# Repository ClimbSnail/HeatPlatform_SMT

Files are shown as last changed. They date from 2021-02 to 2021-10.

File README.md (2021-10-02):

# HeatPlatform_SMT
DIY个人分体式SMT平板加热台。ps:二代已经在开发中了 https://github.com/ClimbSnail/SuperHeat

Github项目最新地址[链接](https://github.com/ClimbSnail/HeatPlatform_SMT) https://github.com/ClimbSnail/HeatPlatform_SMT

Gitee地址（可能不是最新的）[链接](https://gitee.com/ClimbSnailQ/HeatPlatform_SMT) https://gitee.com/ClimbSnailQ/HeatPlatform_SMT

Bilibli视频预览[链接](https://www.bilibili.com/video/BV1ky4y1m7ZF) https://www.bilibili.com/video/BV1ky4y1m7ZF

HeatPlatform_Entity

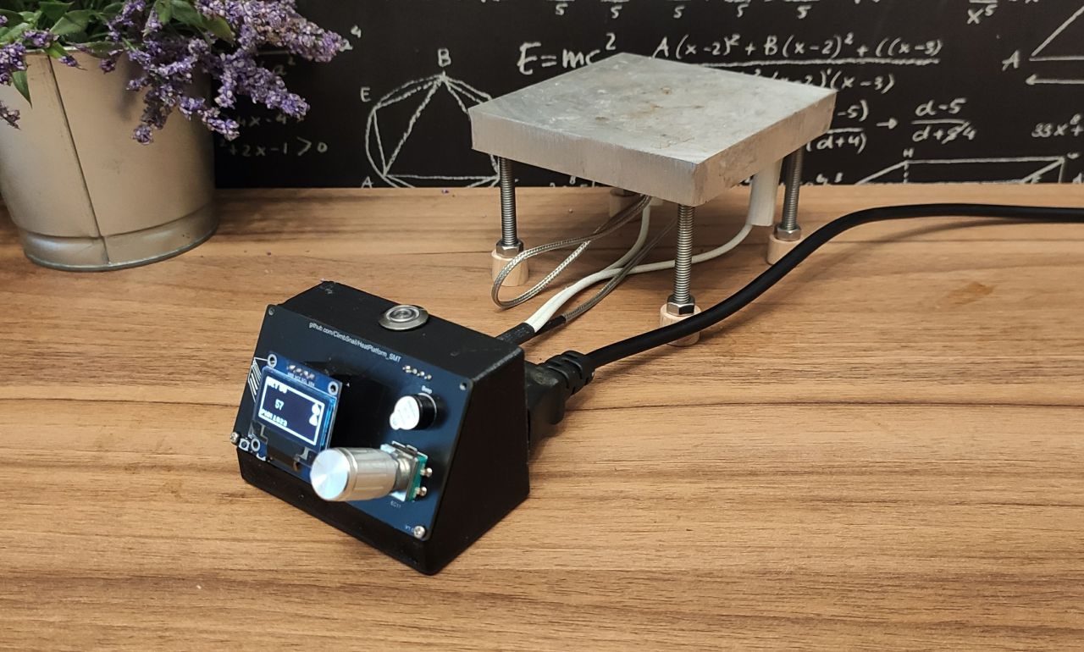
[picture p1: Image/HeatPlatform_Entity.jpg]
HeatPlatform_Entity


##### 免责声明
由于本项目涉及AC220电压，谨慎触碰可控硅附件的走线，只建议有经验的伙伴制作。本人不负责任何由于本项目所引发的安全问题。

### 项目起因

平板加热台可以方便手工对PCB进行贴片焊接。本人是一名北漂软件工程师，同时也是一名电子爱好者，为了搬家时方便，工具的选择总是偏向于便捷化。网络上成品的平板加热台往往较为厚重，故自己动手实现一台。

### 交流群
添加这个qq群`148563337`，需要的朋友多的话，可以考虑一起做。

### 功能介绍
1. 使用PID控制算法，控制器的控温范围为室温~1000摄氏度。（实际温度上限需考虑加热台材料）
2. 目前稳定支持2000w功率的加热板。（可修改为支持更大功率的）
3. 屏幕使用0.96寸的OLED（SSD1306）液晶显示屏。
4. 使用旋转编码器代替按键式操作，提高用户体验。
5. 支持温度曲线的控制。（即将支持）

### 工程包含
1. B站全套自作教程（等待更新）。Bilibli视频[链接](https://www.bilibili.com/video/BV1ky4y1m7ZF) https://www.bilibili.com/video/BV1ky4y1m7ZF
2. 基于ESP8266的温控系统。
3. 控温系统的硬件控制电路。
4. 控制器的外壳3D结构图。
5. 一键刷机工具。

# ESP8266温控器

HeatPlatform_PCB

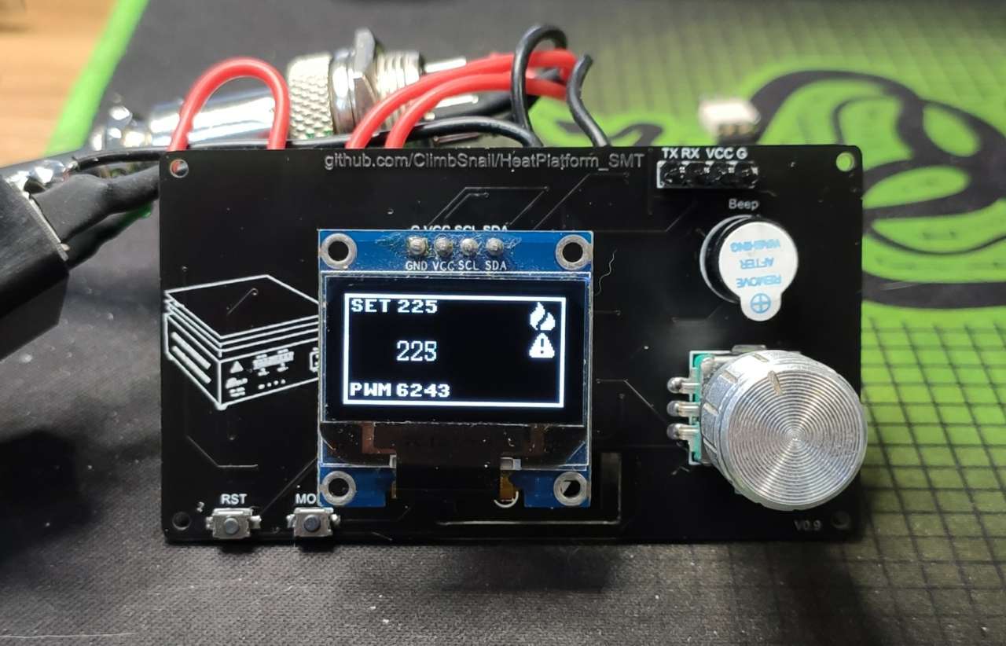
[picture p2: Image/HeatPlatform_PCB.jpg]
HeatPlatform_PCB


HeatPlatform_PCB_Back

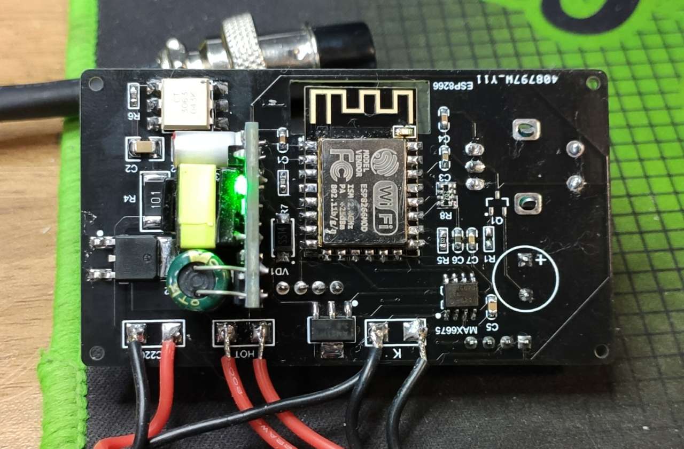
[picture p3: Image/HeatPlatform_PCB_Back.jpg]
HeatPlatform_PCB_Back


1. 总体使用AC220的铝加热板。控温器的温度范围是室温~1000摄氏度，当前铝加热板最好不要超过400度。
2. 主控使用的是ESP8266-12F。
3. 使用MAX6675驱动K型热电偶。
4. 使用PID控制算法控制双向可控硅的导通状态。
5. 使用5脚的EC11旋转编码器作为用户操作的按钮。

### 硬件设计要点
1. 天线附近要保持足够的净空区，否则影响天线的性能。
2. bootloader启动加载程序时，GPIO0为低电平，则进入固件烧录模式。
3. 正常启动时，GPIO0高、GPIO2高、GPIO15低、EN高、RST高。
4. GPIO16不支持中断、PWM、I2C以及One-Wire功能，只能作为普通的输入、输出端口。
5. 光耦的输入触发信号电流要大于5ma，不然光耦的输出端将不能导通。
6. 光耦信号的输出端要接可控硅的1脚。

### 控制器安装说明
1. 热电偶选择K型，最好选择带金属外皮的。
2. 加热台推荐使用铝加热台（纯电阻稳定）。
3. 航空头推荐使用GX16-8的（GX12安全间距不够，8脚是为了后期升级准备）。
4. `AC220`标识的接口连接AC220V的市电。不分零线火线（建议靠外侧的焊盘接火线）。
5. `HOT`是连接加热板的接口，随意接，不分正负。
6. `K`为连接K型热电偶的接口，靠近`AMS1117`稳压芯片那端为负极，改处也是同时用来接地使用（也可不接地）。
7. 航空头接线标准推荐。
	* 2、8脚接GND。
	* 1脚接热电偶正极。
	* 3、4目前留空。
	* 5目前留空。
	* 6、7接加热板供电线。

### 固件刷写
1. 使用USB-TTL下载器链接板子的下载接口（已标识引脚，RXD TXD需要反接）。
2. 本工程附送"一键刷机工具"，双击工具无需任何操作即可刷机。

注：旧版的micropython版本的刷机参考`Software`目录下的`README.md`

### 操作说明
在加热台控制界面长按旋转编码器按钮1秒（实际可能要2s），即可进入设置界面。设置界面长按旋钮1s即可退回加热控制界面。

在设置界面中："空心三角形"为未选中，此时可以切换设置项，按下旋钮即变成选中状态。"实心三角形"未选中状态，可对通过旋钮对选中的设置项进行设置，按下即为"取消选中"。

```
设置界面参数详解：
ST: 开机后的默认"目标温度"，默认值为20

MD: 模式(预留给后期版本固件使用)

DC: 名为"Encoder direction"旋转编码器的方向。0为默认方向，1为方向。

ET: 名为"Error Temperature"实际与显示的温度差，校准时使用。
	ET = 读取的温度-实际真实温度，ET校准时请设置为0，
	然后开启后观察屏幕的温度（读取的温度），在加热状态下 真实温度就等于室温（实际真实温度），进而求得ET，然后设置。

OT: 名为"Overflow Temperature"检测到的温度超出设置温度多少度时报警。
	常规值都为正数，当然也可以为负数。

Ptv: 名为"PID  Value"PID接近设定值多少度时开始调控。
	PTC加热板建议设置成10（度），普通铝板设置为3（度）。
	注：通常值设定与PID参数相关。
	
Kp: PID的p参数。步进为0.1，最大值为9.9，且不能设置为负数。
Ki: PID的i参数。步进为0.1，最大值为9.9，且不能设置为负数。
Kd: PID的d参数。步进为0.1，最大值为9.9，且不能设置为负数。
Kt: PID的t参数，表示PID的控制周期（秒）。步进为0.1，最大值为9.9，且不能设置为负数。

DF: 名为"Default"，表示默认值，短按即可将参数恢复到固件默认设置。

SR: 名为"Save and Reset"保存并重启，短按该项，加热台立即进入重启状态（大约1s后重启），
	所有当前页面的设置参数将会被保存。
```

### 资料
[PID动画演示](https://rossning92.github.io/pid-simulation/)

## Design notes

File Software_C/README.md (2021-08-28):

#### 参考资料
###### EC11编码器
https://www.geek-workshop.com/thread-28165-1-1.html

###### 定时器
https://github.com/khoih-prog/TimerInterrupt_Generic

https://github.com/khoih-prog/ESP8266TimerInterrupt

##### 打包刷机工具
`pyinstaller -F HeatPlatform_tool.py`

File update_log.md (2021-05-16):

### 更新日志

##### 软件
版本 | 更新日期 | 更新说明
:-:|:-:|:-:
v1.0 | 20200213 | 第一版
v1.0.1 | 20210403 | 增加升温完成蜂鸣器的提示，修改编码器的驱动增强操作
v1.0.5 | 20210517 | 增加`surface.py`界面、修改`ssd1306_esp.py` `main.py`的bug

##### 硬件
版本 | 更新日期 | 更新说明
:-:|:-:|:-:
v1.0 | 20200228 | 正式版本
v1.1 | 20200410 | PCB中增加可控硅电路的开窗以及覆铜

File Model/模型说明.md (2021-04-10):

### 模型说明

1. 航空头选用的是GX16-8。
2. 开关使用的是AC220的船型开关，开孔尺寸为19*13mm。
3. 品字接口是不带耳的，开孔尺寸为22*27mm。
4. 固定PCB板的螺丝为M2。

注: 由于外壳需要安装PCB面板，3D打印时材料收缩性不同，可能会出现尺寸不刚好的问题。我使用PLA打印时，长设置为102%，宽为102%。

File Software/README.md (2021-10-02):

### 固件刷写

##### 完全刷写
1. 使用USB-TTL下载器链接板子的下载接口（已标识引脚，RXD TXD需要反接）。
2. `uPyCraft`是代码编写工具，同时也是固件刷写工具，打开`uPyCraft`工具，会提示安装字体（随意安装就行）。
3. 打开软件后，选择工具栏`Tools`->`BurnFirmware`，打开固件烧录的提示框。
	* `board`选择`esp8266`
	* `burn_addr`保持默认
	* `erase_flash`可以选择`yes`
	* `com`选择你TTL下载器的`com口`
	* `Firmware_Choose`中选择`Users`，然后点击`Choose`去选择`Firmware`文件夹中找后缀名为`bin`的固件。
4. 点击`OK`后，弹出刷写固件的页面。
5. 可以看到进度条始终不动。这时按住控制板上的旋钮，接着按下`RST`键（之后松开），紧接着松开刚刚按住的旋钮。这时候可以看到`EraseFlash`进度条开始变化了。
6. 等`EraseFlash`进度条走完，会发现`Burn`进度条卡住了，这时候再按住旋钮，然后再按一下`RST`松开，之后再松开旋钮按键，等进度条走完就刷写成功了。
7. 选择`Tools`->`Serial`中下载器对应的端口之后，下方输出区出现`>>`就表示`uPyCraft`工具自动连接了我们的控制器，即表示第6步的固件刷写过程是成功的。
8. 上传代码文件：双击`uPyCraft`工具左侧的`workSpace`文件夹（第一次），会让选择一个文件夹，这时我们浏览到`Software`文件夹的上级目录就行。随后点击`File`->`reflush`刷新下左侧的文件目录。再次点开`workSpace`就可以看到`Software`里的程序文件了。
9. 双击打开任意除`main.py`外的文件，点击`Tools`->`Download`，若上传成功 可以在下方的输出区看到`download ok`字样。重复此过程，使`Software`中的文件依次上传。
10. `uPyCraft`工具左侧的`device`目录中显示的是当前控制器中已有的程序，由此可以判断文件是否上传成功。在等到上传结束，最后再上传`main.py`的文件。
11. 完成。控制板接上铝加热板就可以工作了。当然不需要铝加热板也可以简单接上oled屏幕，重新上电或者按下RST复位，看oled是否正常显示。

##### 更新程序
更新程序是建立在之前进行过_"固件刷写"_操作。

按住控制器上的`MODE`按键，然后按下`RST`松开，`MODE`按键需等待背部ESP8266的指示灯常亮`（5-7s）`左右再松开，控制器即可进入程序更新模式。可跳过前6步骤，直接从第7步开始 更新想要更新的程序文件。

### 在线更新固件脚本（在计划中）
1. 使用webrepl进行更新固件(双击webrepl工具里的"webrepl.html")
2. [链接](ws://192.168.4.1:8266/) ws://192.168.4.1:8266/（链接加热控制器的wifi后方可链接）
3. 密码预设为`88888888`（在config.json文件中已注明）

### 学习资料传送门
1. [教程 in Github](https://github.com/lvidarte/esp8266/wiki)
2. [ESP8266固件](http://micropython.org/download#esp8266)
3. [uPyCraft IDE](http://docs.dfrobot.com.cn/upycraft/)
4. [官方参考文档](https://docs.micropython.org/en/latest/esp8266/quickref.html#pins-and-gpio)
5. [MicroPython API](https://makeblock-micropython-api.readthedocs.io/zh/latest/library/)

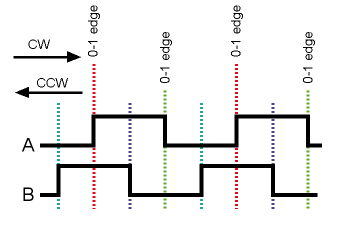
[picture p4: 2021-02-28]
Image/EC11_sequential.jpg

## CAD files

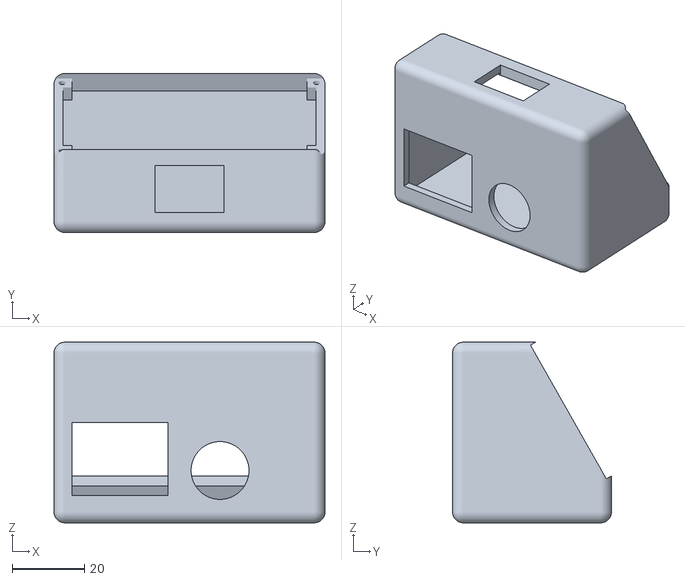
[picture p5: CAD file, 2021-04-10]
Model/HeatPlaform_SMT.stl
75.0 x 44.0 x 50.0

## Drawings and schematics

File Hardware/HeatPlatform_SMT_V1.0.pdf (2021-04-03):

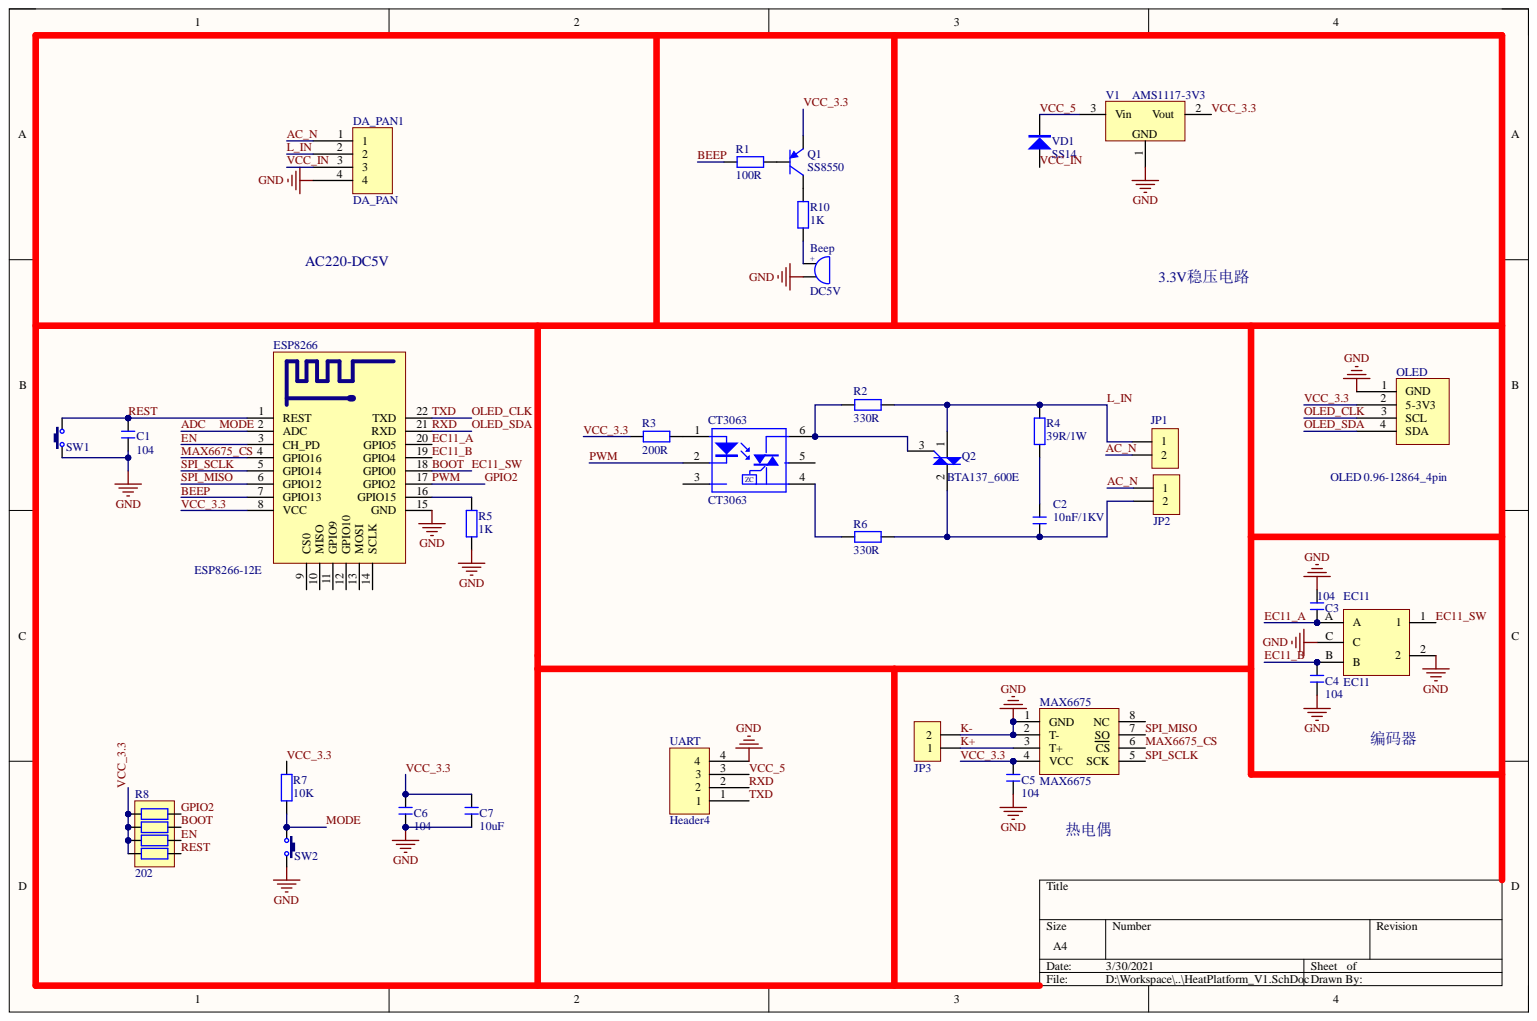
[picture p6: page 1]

ESP8266 | R2 | GND OLED

REST 1

SCLK 14 GND 15 GPIO15 16 GPIO2 17 GPIO0 18 GPIO4 19 GPIO5 20 RXD 21 TXD 22

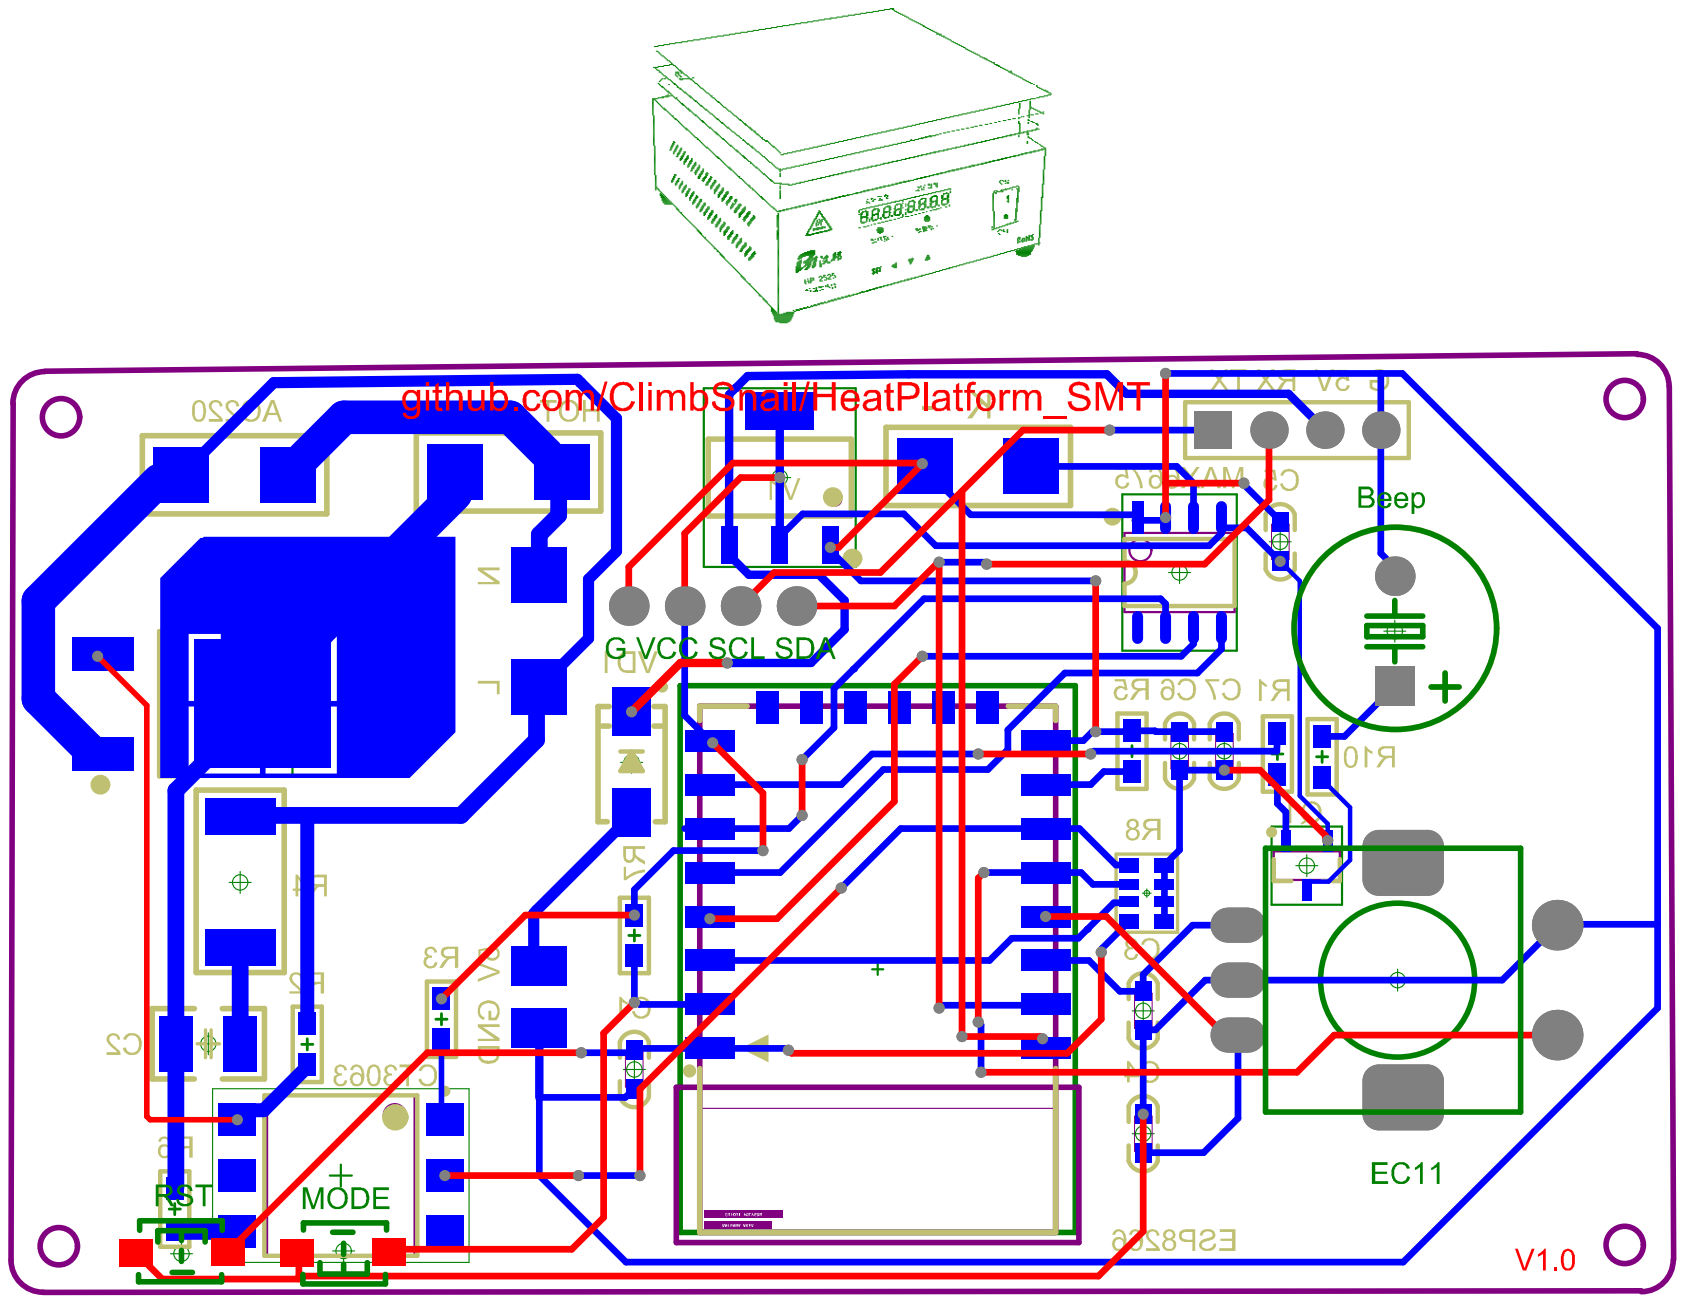
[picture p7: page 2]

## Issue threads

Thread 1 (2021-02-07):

这个加热盘最高能到几度呀？

ChenJBBB, 2021-02-07:
我是想搞一个加热台来拆像ESP32 ESP8266这种大SMD封装模块，用热风枪不好搞，SMT贴片时候好像也可以用用。不知道像拆这个板子是的ESP8266-12F容易吗（套娃，我拆我自己）。
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
还有PTC的加热板买的多大几W的，方便粘贴一下链接吗。

然后我觉得这个板子这边
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
应该开窗一下去掉阻焊层，到时候加手动加锡，增大能通过的电流。

ClimbSnail, 2021-02-10:
1. 拆esp32（底部带散热盘）这种比较容易的。
2. 使用的不是PTC加热板。PTC加热板温度不是线性变化的。这里用的是发热丝型的铝加热板。150*100mm的大概35块钱。
3. 是的，新版本阻焊层已经开窗了，但是图片还未更新。初步计算板子能承受10A的电流，2200w（220V）。
后期可以添加这个qq群148563337，如果有需要可以考虑一起做。

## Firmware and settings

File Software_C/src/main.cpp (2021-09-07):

#include <Arduino.h>

#include "ESP8266TimerInterrupt.h"
#include "ESP8266_ISR_Timer.h"

#include "common.h"
#include "max6675.h"
#include "knobs.h"
#include "buzzer.h"
#include "pid.h"
#include "surface.h"
#include "main.h"

MAX6675 max6675(14, 12, 16);
Knobs knobs(4, 5, 0);
Buzzer buzzer(13, 10);
PID pid_contorller(4.5, 0.15, 0.2, 0.2);
Surface surface(3, 1);

// Init ESP8266 timer 0
ESP8266Timer iTimer;
// Init BlynkTimer
ESP8266_ISR_Timer ISR_Timer;
#define HW_TIMER_INTERVAL_MS 1L

#define SWITCH_TIME 1000      // 检测长按的时间
unsigned long previousMillis; // 上次刷新屏幕的时间戳

// 以下为运行时的参数
#define BUFFER_MAX_SIZE 10 //
int buffer_size = 5;       // 缓冲区的实际大小
int buf_index = 0;
int buf_sum = 0; // 需要在setup中初始化赋值
volatile boolean temperature_err_flag = true;
int temperature_buf[BUFFER_MAX_SIZE] = {20, 20, 20, 20, 20,
                                        20, 20, 20, 20, 20};

volatile int temperature_setting = 0;     // 设定的目标温度
volatile int temperature_now = 4095;      // 当前温度
volatile boolean start_read_temp = false; // 标志是否开始读取温度
volatile boolean pid_enable = false;      // 标志pid控制是否开启

KeyInfo knobs_val = {0, 0};            // 按键的值
volatile boolean is_knobs_opt = false; // 按键是否操作

#define PWM_FREQ 5                    // pwm的频率/
#define PWM_PRECISION 200             // pwm的精度
#define PWM_PIN 2                     // pwm的pin引脚
volatile int out_pwm = PWM_PRECISION; // 输出的PWM 199为最大值
volatile int pwm_count = 0;           // pwm的计数值

int process_index = 0;    // 控制页面
#define PROCESS_MAX_NUM 2 // 页面最大数
void (*pProcessArray[PROCESS_MAX_NUM])(int type, int16_t value) = {
    main_process, setting_process};

void IRAM_ATTR TimerHandler()
{
    static bool toggle = false;
    static bool started = false;
    static int timeRun = 0;

    ISR_Timer.run();

    // // Toggle LED every LED_TOGGLE_INTERVAL_MS = 2000ms = 2s
    // if (++timeRun == (LED_TOGGLE_INTERVAL_MS / HW_TIMER_INTERVAL_MS))
    // {
    //     timeRun = 0;

    //     if (!started)
    //     {
    //         started = true;
    //         pinMode(LED_BUILTIN, OUTPUT);
    //     }

    //     //timer interrupt toggles pin LED_BUILTIN
    //     digitalWrite(LED_BUILTIN, toggle);
    //     toggle = !toggle;
    // }
}

typedef void (*irqCallback)();

void interrupt_read_temperature()
{
    start_read_temp = true;
}

void interrupt_check_knobs()
{
    is_knobs_opt = true;
}

void interrupt_ctrl_pid()
{
    pid_enable = true;
}

void interrupt_pwm()
{
    if (0 == pwm_count)
    {
        digitalWrite(PWM_PIN, HIGH);
    }
    if (out_pwm == pwm_count)
    {
        digitalWrite(PWM_PIN, LOW);
    }
    pwm_count = (pwm_count + 1) % PWM_PRECISION;
}

#define NUMBER_ISR_TIMERS 5

// You can assign any interval for any timer here, in milliseconds
uint32_t TimerInterval[NUMBER_ISR_TIMERS] = {
    buzzer.m_cycle_time,
    200L,
    150L,
    200L,
    1000L / PWM_FREQ / PWM_PRECISION};

irqCallback irqCallbackFunc[NUMBER_ISR_TIMERS] = {
    buzzer.timer_handler, interrupt_read_temperature,
    interrupt_check_knobs, interrupt_ctrl_pid, interrupt_pwm};

// 加热板的主控制页面
void main_process(int type, int16_t value)
{
    switch (type)
    {
    case NONE_TYPE:
    {
        surface.set_temperature(temperature_setting, temperature_now, out_pwm);
        surface.display_main();
    }
    break;
    case ENCODER_TYPE:
    {
        int speed = int(fabs(value / 2)) + 1;
        temperature_setting += (speed * value);
        // 限制温度调整范围
        if (temperature_setting < 0)
        {
            temperature_setting = 0;
        }
        if (temperature_setting > 1000)
        {
            temperature_setting = 1000;
        }
    }
    break;
    case BUTTON_TYPE:
    {
        if (value > SWITCH_TIME)
        {
            process_index = (process_index + 1) % PROCESS_MAX_NUM;
        }
    }
    break;
    default:
        break;
    }
}

// 设置页面
void setting_process(int type, int16_t value)
{
    static uint8 setting_info_index = 0;
    static boolean setting_info_choose = false; // 不为选中状态

    switch (type)
    {
    case NONE_TYPE:
    {
        // surface.set_temperature(temperature_setting, temperature_now, out_pwm);
        // surface.display_main();
    }
    break;
    case ENCODER_TYPE:
    {
        if (setting_info_choose)
        {
            // 设置数据
            switch (setting_info_index)
            {
            case 0:
            {
                user_data.save_temperature += value;
            }
            break;
            case 1:
            {
                user_data.mode += value;
            }
            break;
            case 2:
            {
                // +150（2的整倍数就行） 的作用主要为了让数据不会出现负数
                user_data.direction = (user_data.direction + 150 + value) % 2;
            }
            break;
            case 3:
            {
                user_data.err_temperature += value;
            }
            break;
            case 4:
            {
                user_data.overflow_temperature += value;
            }
            break;
            case 5:
            {
                user_data.pid_threshold_value += value;
            }
            break;
            case 6:
            {
                user_data.kp += (0.1 * value);
            }
            break;
            case 7:
            {
                user_data.ki += (0.1 * value);
            }
            break;
            case 8:
            {
                user_data.kd += (0.1 * value);
            }
            break;
            case 9:
            {
                user_data.kt += value;
            }
            break;
            case 10:
            {
                // 恢复默认
            }
            break;
            case 11:
            {
                // 保存并重启
            }
            break;
            }
        }
        else
        {
            // +120（USER_SET_PARAM_NUM + 2的整倍数就行） 的作用主要为了让数据不会出现负数
            setting_info_index = (setting_info_index + 120 + value) % (USER_SET_PARAM_NUM + 2);
        }
    }
    break;
    case BUTTON_TYPE:
    {
        if (value > SWITCH_TIME)
        {
            // 切换页面
            process_index = (process_index + 1) % PROCESS_MAX_NUM;
        }
        else
        {
            if (10 == setting_info_index)
            {
                init_user_data();
                return;
            }
            else if (11 == setting_info_index)
            {
                user_data.save_temperature = temperature_setting;
                // 保存并重启
                iTimer.disableTimer();
                ISR_Timer.disableAll();
                delay(100);
                save_config();
                ISR_Timer.enableAll();
                iTimer.enableTimer();
                return;
            }
            // 设置当前设置项为选中状态
            setting_info_choose = !setting_info_choose;
        }
    }
    break;
    default:
        break;
    }
    double setting_info_data[USER_SET_PARAM_NUM] = {
        user_data.save_temperature, user_data.mode,
        user_data.direction, user_data.err_temperature,
        user_data.overflow_temperature, user_data.pid_threshold_value,
        user_data.kp, user_data.ki, user_data.kd, user_data.kt};

    surface.set_setting(USER_SET_PARAM_NUM, setting_info_data,
                        setting_info_index, setting_info_choose);
}

void setup()
{
    // put your setup code here, to run once:
    // Serial.begin(74880);
    // Serial.print(F("Starting OK."));

    for (int pos = 0, buf_sum = 0; pos < buffer_size; ++pos)
    {
        buf_sum += temperature_buf[pos];
    }

    load_config();
    temperature_setting = user_data.save_temperature; // 设定的温度
    pid_contorller.set_pid_param(user_data.kp, user_data.ki, user_data.kd, 0.2);

    // 初始化PWM引脚
    pinMode(PWM_PIN, OUTPUT);

    // Interval in microsecs
    bool ret = iTimer.attachInterruptInterval(HW_TIMER_INTERVAL_MS * 1000, TimerHandler);
    // if (true == ret)
    // {
    //     Serial.print(F("Starting ITimer OK."));
    // }
    // else
    //     Serial.println(F("Can't set ITimer. Select another freq. or timer"));

    // Just to demonstrate, don't use too many ISR Timers if not absolutely necessary
    // You can use up to 16 timer for each SAMD_ISR_Timer
    for (uint16_t i = 0; i < NUMBER_ISR_TIMERS; i++)
    {
        ISR_Timer.setInterval(TimerInterval[i], irqCallbackFunc[i]);
    }

    buzzer.set_beep_time(700); // 开机提示音
    surface.init();
    // surface.set_temperature(temperature_setting, temperature_now, out_pwm);
}

void read_temperature()
{
    if (false == start_read_temp)
    {
        return;
    }

    start_read_temp = false;
    // user_data.err_temperature 为用户设定的温度误差
    int temp = max6675.read_temperature_mock() - user_data.err_temperature;
    if (temp == 4095)
    {
        temperature_err_flag = true;
        return;
    }
    temperature_err_flag = false;

    buf_sum = buf_sum - temperature_buf[buf_index];
    temperature_buf[buf_index] = temp;
    buf_sum = buf_sum + temperature_buf[buf_index];

    buf_index = (buf_index + 1) % buffer_size;
    temperature_now = buf_sum / buffer_size;
}

void pid_ctrl()
{
    if (false == pid_enable)
    {
        return;
    }

    pid_enable = false;

    if (true == temperature_err_flag)
    {
        // 未接加热板
        out_pwm = PWM_PRECISION;
        return;
    }

    if (temperature_setting - temperature_now > user_data.pid_threshold_value)
    {
        // 还未到达PID开始调控的温度范围
        out_pwm = 0; // 最大值输出
        pid_contorller.set_data(3, 0);
    }
    else if (temperature_now > temperature_setting)
    {
        // 当前温度大于实际温度
        out_pwm = PWM_PRECISION; // 最小值输出
        pid_contorller.set_data(0, 0);
        if (temperature_now - temperature_setting > user_data.overflow_temperature && temperature_now > 50)
        {
            // 报警提示音
            buzzer.set_beep_time(700);
        }
    }
    else
    {
        if (temperature_setting == temperature_now)
        {
            // 报警
        }
        int ret_out = pid_contorller.get_output(temperature_setting, temperature_now);
        // Serial.print("\nret_out:");
        // Serial.println(ret_out);
        // 以下处理pwm的高低电平反向
        if (ret_out > 0)
        {
            if (ret_out > PWM_PRECISION - 1)
                out_pwm = 0;
            else
                out_pwm = PWM_PRECISION - ret_out;
        }
        else
            out_pwm = PWM_PRECISION;
    }
}

void knobs_deal()
{
    if (false == is_knobs_opt)
    {
        return;
    }

    is_knobs_opt = false;

    knobs_val = knobs.get_data();
    if (0 != knobs_val.pulse_count)
    {
        // 刚开始process_index=0，首页指向控制加热板的控制页面
        if (1 == user_data.direction)
        {
            // user_data.direction 为编码器旋转方向的设置
            knobs_val.pulse_count = -knobs_val.pulse_count;
        }
        pProcessArray[process_index](ENCODER_TYPE, knobs_val.pulse_count);
        buzzer.set_beep_time(50);
    }
    if (0 != knobs_val.switch_status)
    {
        if (knobs_val.switch_time > SWITCH_TIME)
        {
            buzzer.set_beep_time(1000);
        }
        else
        {
            buzzer.set_beep_time(200);
        }
        pProcessArray[process_index](BUTTON_TYPE, knobs_val.switch_time);
    }
}

void loop()
{
    read_temperature();
    pid_ctrl();
    knobs_deal();
    if (doDelayMillisTime(500, &previousMillis, false))
    {
        // 刚开始process_index=0，首页指向控制加热板的控制页面
        pProcessArray[process_index](NONE_TYPE, 0); // 更新动作
    }
}

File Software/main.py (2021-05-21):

import time
# from wifi import WifiController
from knobs import EC11
from max6675 import MAX6675
from ssd1306_esp import SSD1306_I2C
from pid import PID
# import webrepl
from machine import Pin, PWM
from machine import Timer
import gc
from surface import Interface


class HeatPlatform():
    """
    加热平台控制主类
    """

    def __init__(self, config_dict, OLED_Status=True):
        self.cfg = config_dict  # 配置文件信息
        self.pwm_out = PWM(Pin(2), freq=5, duty=1023)

        self.max6675 = MAX6675(None, None, None, Pin(16, Pin.OUT))
        # max6675使用的是硬件SPI，会设置GPIO13引脚，若使用GPIO13（蜂鸣器）请后初始化

        self.beep = Pin(13, Pin.OUT)    # 蜂鸣器引脚
        self.beep.value(1)      # 关闭蜂鸣器
        self.beep_flag1 = True
        self.beep_flag2 = False	# 只当编码器值改变时才置为True
        # 安全温度阈值，当 实际温度-与设定温度>self.max_error_temperature 触发报警
        self.max_error_temperature = 30

        self.buf_len = 3
        self.buf_index = 0
        self.temperature_err_flag = True
        self.temperature_buf = [20] * self.buf_len
        self.buf_sum = 20 * self.buf_len

        self.temp_now = self.max6675.read_temperature()
        self.temp_target = 50
        # 进行PID控制的阈值（以致于前期可以持续快速升温）
        self.temp_DValue = 20
        self.pid_enable = False
        self.pid_dt = 300 # PID的调整时间ms
        gc.collect()

        # 创建OLED显示器
        # construct an I2C bus，软件i2c所有接口都适用
        self.interface = Interface(self, Pin(1), Pin(3), OLED_Status)
        self.interface.temperature_now = self.temp_now
        self.interface.temperature_target = self.temp_target
        self.interface.opt_deal()

        # 创建编码器控制对象
        self.knobs = EC11(4, 5, 0)

        # 创建pid控制对象
        # self.pid_contorller = PID(6.0, 18.0, 6.0, self.pid_dt/1000)
        # self.pid_contorller = PID(6.0, 3.0, 10.0, self.pid_dt/1000)
        self.pid_contorller = PID(1.0, 0.3, 6.0, self.pid_dt/1000)

        # 创建蜂鸣器的定时器
        self.beep_start_timer = Timer(-1)  # periodic with 100ms period
        # mode: Timer.ONE_SHOT / Timer.PERIODIC
        self.beep_start_timer.init(period=1000, mode=Timer.PERIODIC,
                             callback=self.start_beep)

        # 创建温度读取的定时器
        self.temperature_timer = Timer(-1)  # periodic with 100ms period
        # mode: Timer.ONE_SHOT / Timer.PERIODIC
        self.temperature_timer.init(
            period=200, mode=Timer.PERIODIC, callback=self.get_temperature)

        # 创建按键检测的定时器
        self.knobs_timer = Timer(-1)  # periodic with 100ms period
        # mode: Timer.ONE_SHOT / Timer.PERIODIC
        self.knobs_timer.init(
            period=200, mode=Timer.PERIODIC, callback=self.check_knobs)

        # 创建pid调节的定时器
        self.adjust_timer = Timer(-1)
        # mode: Timer.ONE_SHOT / Timer.PERIODIC
        self.adjust_timer.init(
            period=self.pid_dt, mode=Timer.PERIODIC, callback=self.adjust_temperature)

        gc.collect()

    def get_temperature(self, timer):
        temperature = self.max6675.read_temperature()
        if temperature == 4095:
            self.temperature_err_flag = True
            return None
        else:
            self.temperature_err_flag = False
        self.buf_sum = self.buf_sum - self.temperature_buf[self.buf_index]
        self.temperature_buf[self.buf_index] = temperature
        self.buf_sum = self.buf_sum + self.temperature_buf[self.buf_index]
        self.buf_index = (self.buf_index+1) % self.buf_len

    def check_knobs(self, timer):
        # increase为一个长度为2的元组 编码脉冲+按键是否按下
        increase = self.knobs.get_data()
        # 跳转到界面里处理按键触发的指令
        self.interface.opt_deal(increase[0], increase[1])

    def start_beep(self, timer):
        """
        蜂鸣器报警
        """
        if self.beep_flag1 == True and self.beep_flag2 == True \
			and self.beep.value() == 1:
            self.beep_flag1 = False
            self.beep_flag2 = False
            self.beep.value(0)
            # 创建蜂鸣器的关闭定时器
            self.beep_end_timer = Timer(-1)  # periodic with 100ms period
            # mode: Timer.ONE_SHOT / Timer.PERIODIC
            self.beep_end_timer.init(
                period=700, mode=Timer.ONE_SHOT, callback=self.end_beep)

    def end_beep(self, timer):
        """
        蜂鸣器报警
        """
        self.beep.value(1)
       

    def adjust_temperature(self, timer):
        if self.temperature_err_flag == True:
            str_temp_now = "XXXX"
            self.pwm_out.duty(1023)
            self.interface.temperature_now = str_temp_now
            self.interface.pwm = 1023
            self.interface.show()
            return None

        self.interface.temperature_now = int(self.buf_sum/self.buf_len)
        self.temp_now = self.interface.temperature_now
        str_temp_now = str(self.temp_now)
        pwm_val = None  # 输出的PWM值
        if self.temp_target - self.temp_now > self.temp_DValue:
            pwm_val = 0
            #self.pid_enable = False
            self.beep_flag1 = False
            self.pid_contorller.set_data(self.temp_DValue, 0)
        elif self.temp_now > self.temp_target:
            pwm_val = 1023
            #self.pid_enable = False
            if self.temp_now-self.max_error_temperature > self.temp_target:
                # 当温度高于安全温度差，立即报警
                self.beep_flag1 = True  # 蜂鸣器报警标志
                self.beep_flag2 = True  # 蜂鸣器报警标志
            self.pid_contorller.set_data(0, 0)
        else:
            if self.temp_target == self.temp_now:
                self.beep_flag1 = True  # 蜂鸣器报警标志
            #if self.pid_enable == False:
            #    self.pid_enable = True
            out_val = self.pid_contorller.get_output(
                self.temp_target, self.temp_now)

            pwm_val = int(out_val)
            if pwm_val > 0:
                if pwm_val > 1020:
                    pwm_val = 0
                else:
                    pwm_val = 1023-pwm_val
            else:
                pwm_val = 1023
        self.pwm_out.duty(pwm_val)

        self.interface.pwm = pwm_val
        self.interface.show()

    def __del__(self):
        self.temperature_timer.deinit()
        self.knobs_timer.deinit()
        self.adjust_timer.deinit()
        self.temperature_timer.deinit()
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

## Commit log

2021-04-03 修改 EC11编码器
2021-04-10 add model and update HW_v1.1
    [HeatPlatform_V1.1.SchDoc, HeatPlatform_V1.SchDoc]
2021-04-10 修改模型文件
    [HeatPlaform_SMT.stl]
2021-04-17 完善PCB
2021-05-21 精简程序
2021-08-22 create code for C
    [partitions-no-ota.csv]
2021-09-01 修改冲突
2021-09-04 update PCB line
